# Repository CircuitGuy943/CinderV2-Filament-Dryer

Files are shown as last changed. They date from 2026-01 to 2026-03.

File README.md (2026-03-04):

# Cinder Filament Dryer - A fully featured 90W filament dryer for all your drying needs!

The cinder filament dryer is a self managed ecosystem comprising of 2 45W heaters powered from a 90W+ power supply to provide the most heating power possible. In addition to that, there is also space for 3 possible fans with silica gel pouch to aid in the airflow and dryer performance. Equiped with an SHT40 module, you will always be 110% aware of exactly how long your filament will take to dry and at what temperature and with a 90W heater, I can guarantee that won't be long ;). Also comes in a cool, tilted design with a fancy flame aesthetic on the side, it also utilizes a smart locking system that adapts the arm of the spool holder to the width of the spool hole, this way, you can ensure the spool is free to spin properly and doesn't scratch the heating element. And if that isn't enough filament flow for you, there is also a dedicated servo driving system and filament extrusion rate feedback integration that automatically pushes out the strand of filament so that the printer, or you, don't have to worry about printing while drying. Comes with a 128x64 OLED, 3 buttons and an encoder for all your "control panel" needs because, we all love fancy control panels don't we? The frame itself is designed to be easy to print (albeit quite large) and assemble. And not to mention with the amazing aesthetic comes a super cool futuristic, pod like door system that lifts upwars on a big pin hinge to allow you to remove the spools or insert more. And obviously, we don't want tipping dryers so, on another pin hinge, we have a leg that can be bent backwards flush to the device when the dryer is hung on the wall or extended so that it literally doesn't fall over.

Some CAD images:

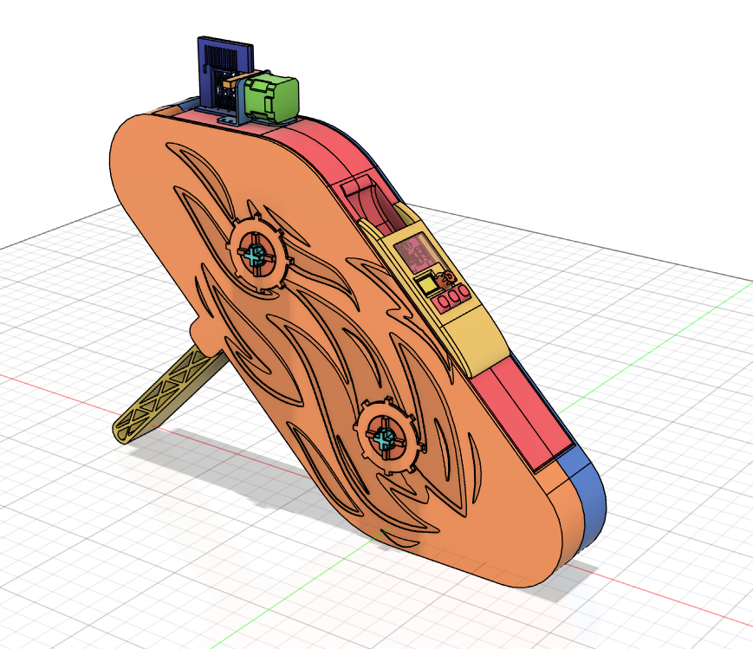
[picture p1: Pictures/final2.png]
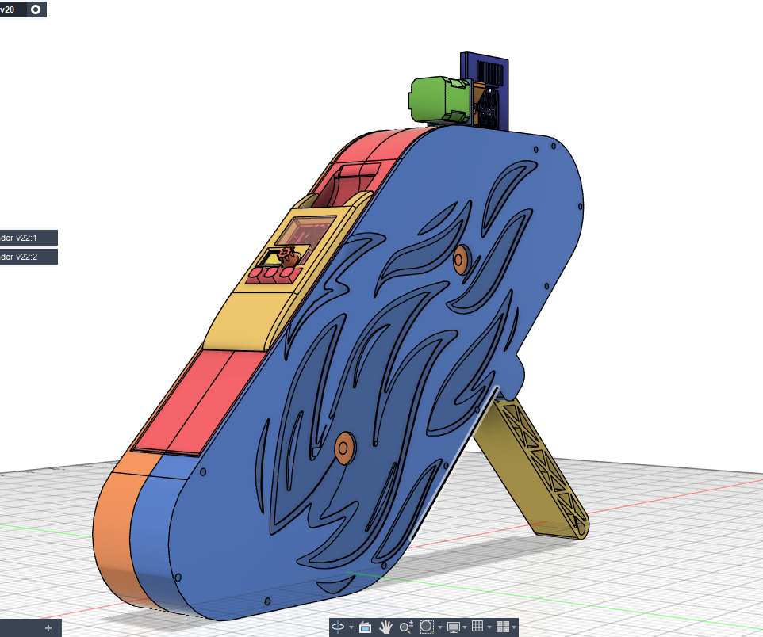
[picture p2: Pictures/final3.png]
 

## Features:
- It drys filament (duh)
- 90W heating power
- OLED display control panel with 3 buttons, encoder and a cool acrylic view panel
- Leg (pretty simple) to hold it from falling backwards
- Fully integrated PCB that drives the 90W heaters, stepper motor driver, OLED, buttons and connectors for all the other sensors.
- Filament pushing system with extruding feedback to maintain proper filament pushing flow
- Easy to assemble
- Airflow powered by 3 5020 fans (LOTS of airflow)
- Spaces for silica gel pouches
- Fancy, cool looking tilted design with flame aesthetics
- Automatic locking system for holding the spool with an arm extendible in diameter <sup>TM</sup>
- PWM control of fans and heater

## PCB
And this is my main PCB. A bit budget restrained otherwise so I had to use some premade sensor modules, the actual flex heater PCB is pretty simple so I won't bother putting it here (but it's in the files):

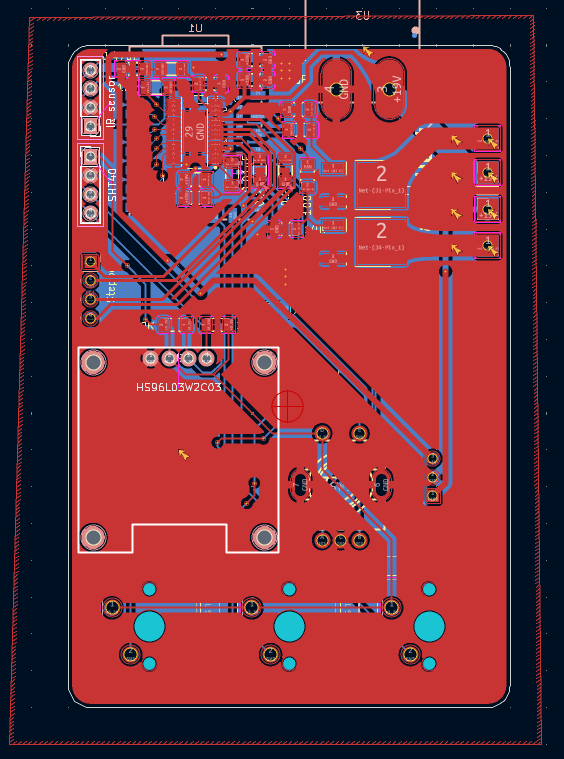
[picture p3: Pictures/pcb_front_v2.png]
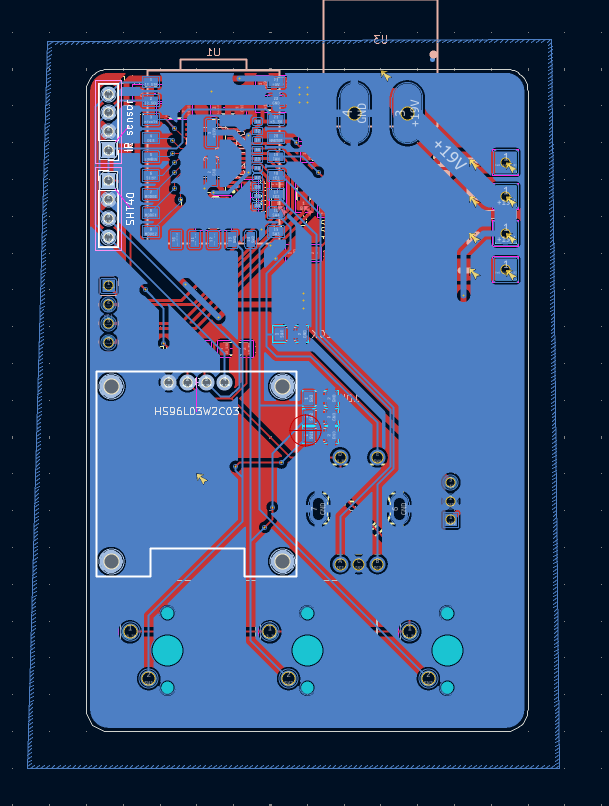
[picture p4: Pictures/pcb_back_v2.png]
  

And the Schematic:

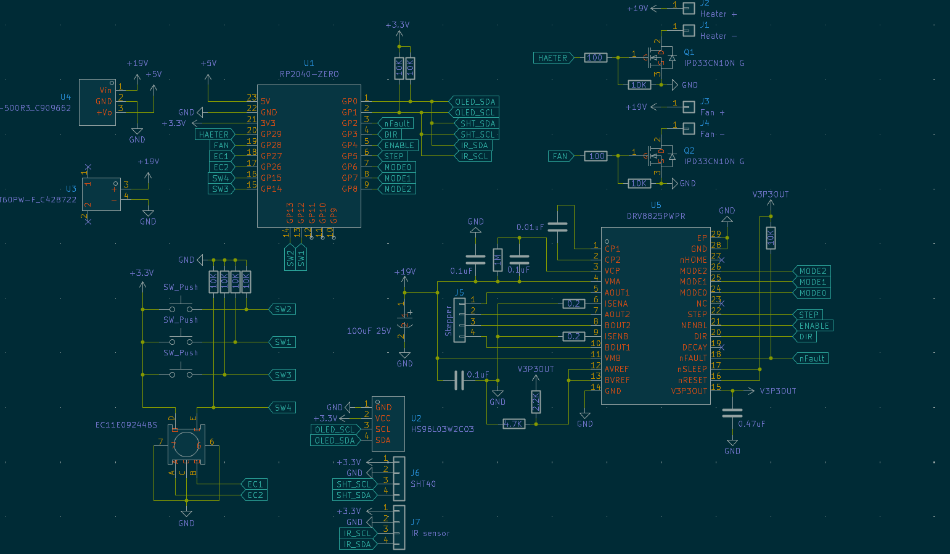
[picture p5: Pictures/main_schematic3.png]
Schematic


And here are some 3D views as well:

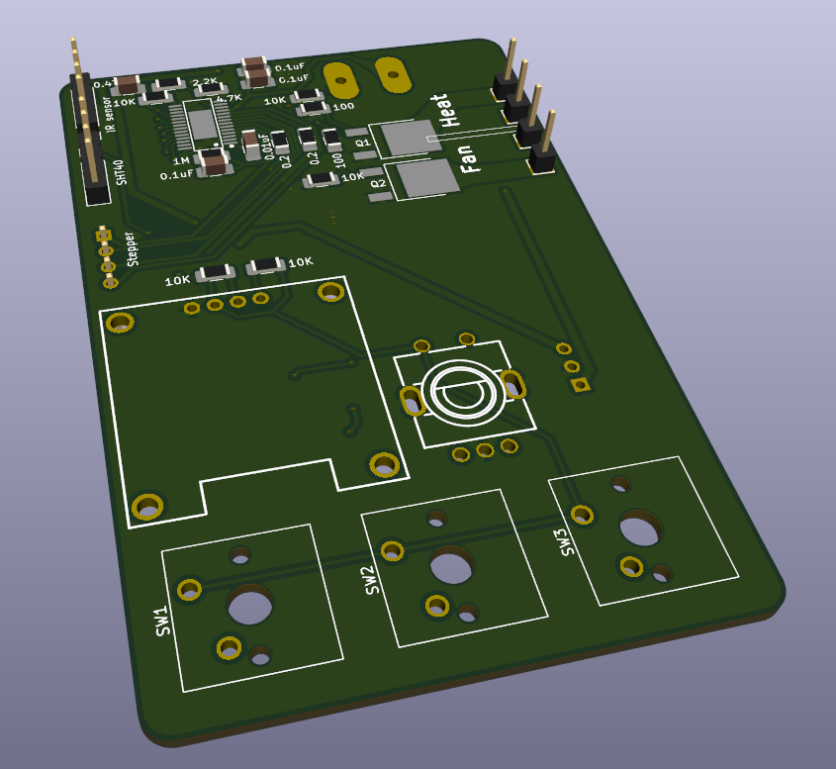
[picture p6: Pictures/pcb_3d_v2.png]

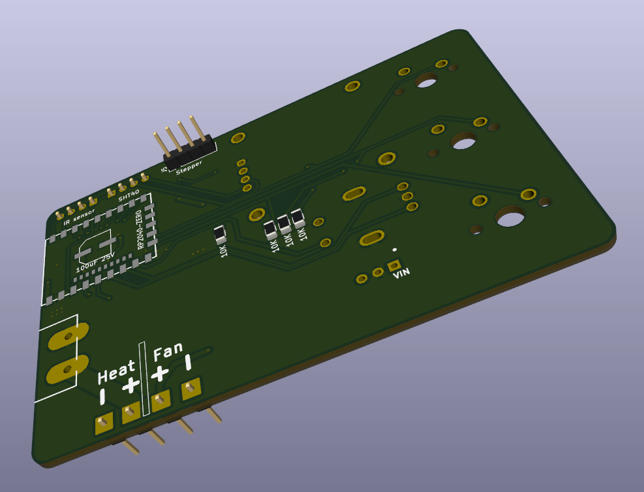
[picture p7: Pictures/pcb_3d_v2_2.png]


## Firmware Overview
At the current moment there is some, untested firmware in there that's supposed to have the dryer functioning but, I don't actually have it yet so I can't test, in future I will program it properly.

## BOM:

- The actual print (alot, probably like 1-2kg+)
- The main PCB (check KiCad files for all the components and external modules)
- 3 5020 fans
- A stepper motor
- Some lasercut acrylic
- MX keycaps (3)
- Some M2 heated inserts and bolts to hold the whole thing togethor

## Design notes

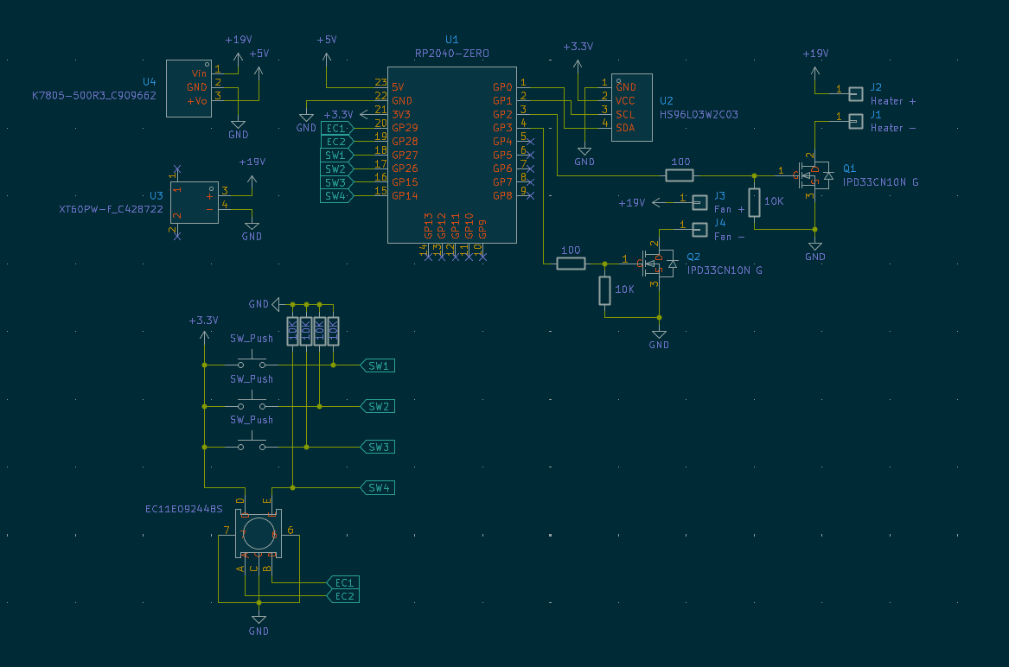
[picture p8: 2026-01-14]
Pictures/main_schematic2.png

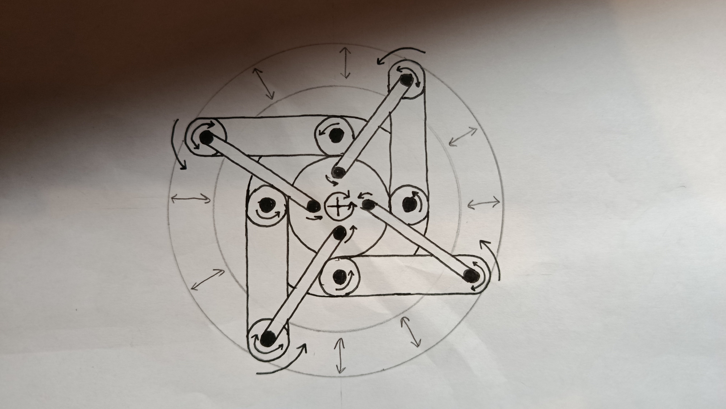
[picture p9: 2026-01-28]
Pictures/design3.jpg

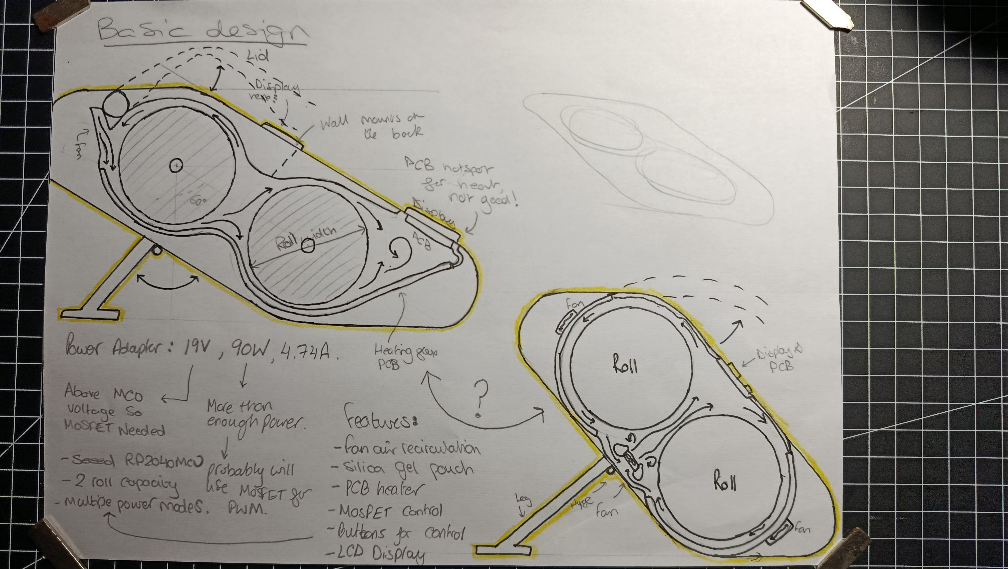
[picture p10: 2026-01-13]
Pictures/design.jpg

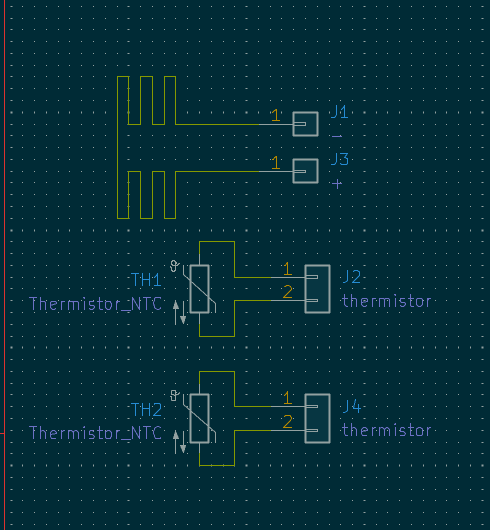
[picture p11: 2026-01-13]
Pictures/flex_heater_schematic.png

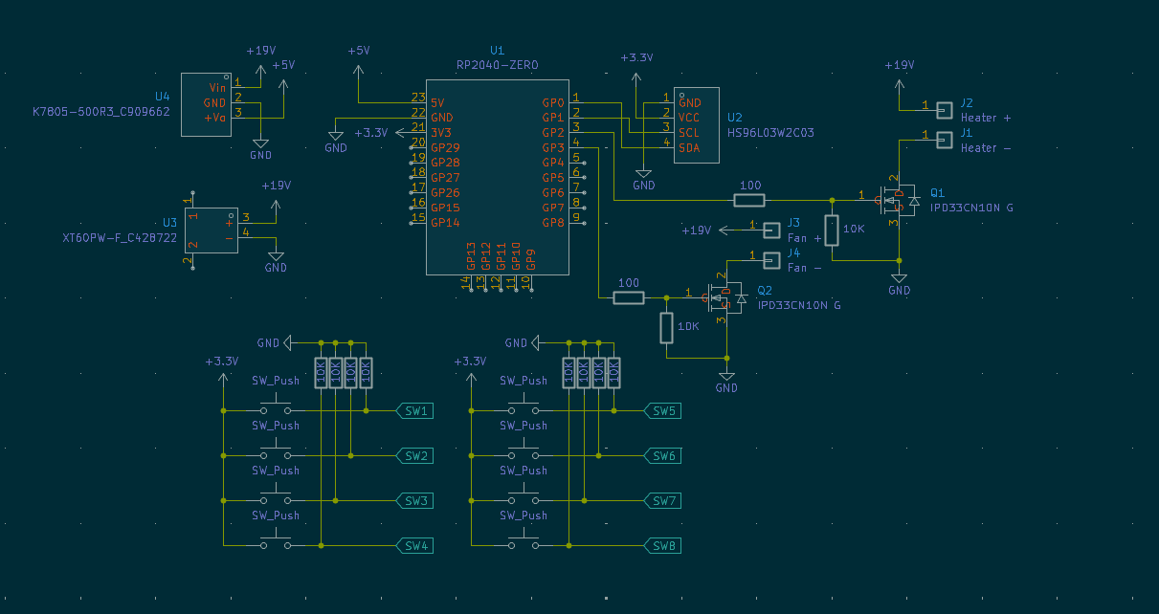
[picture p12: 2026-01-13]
Pictures/main_schematic.png

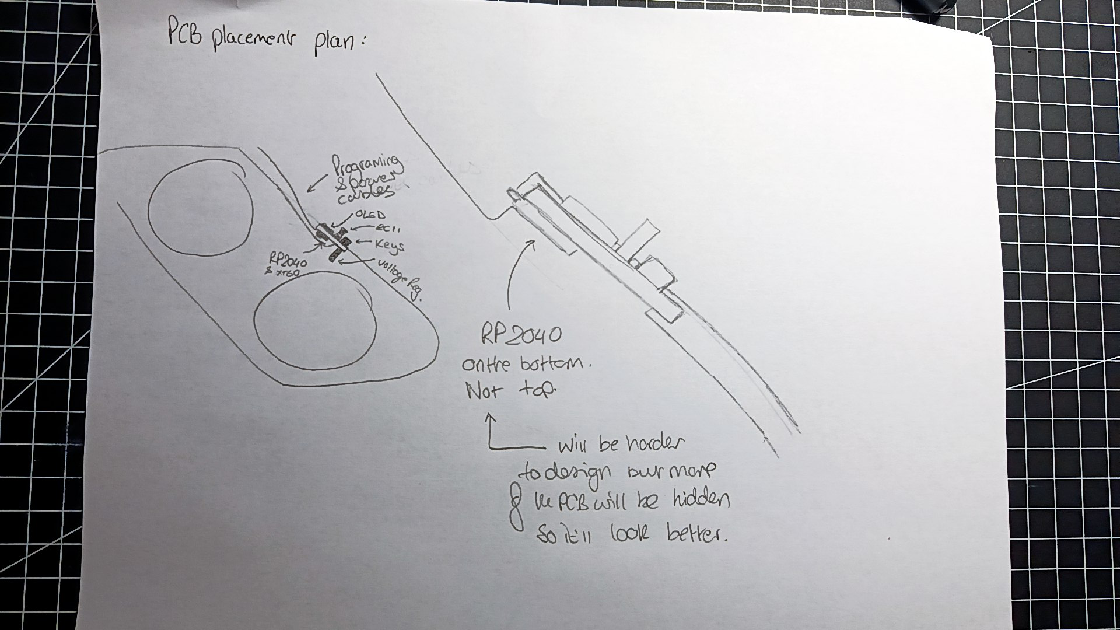
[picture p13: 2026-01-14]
Pictures/design 2.jpg

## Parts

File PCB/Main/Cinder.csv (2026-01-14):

Id | Designator | Footprint | Quantity | Designation | Supplier and ref
1 | J1,J4 | PinHeader_1x01_P2.54mm_Vertical | 2 | -
2 | J2,J3 | PinHeader_1x01_P2.54mm_Vertical | 2 | +
3 | SW1,SW2,SW3 | SW_Cherry_MX_1.00u_PCB | 3 | SW_Push
4 | U1 | COMM-SMD_RP2040-ZERO | 1 | RP2040-ZERO
5 | U2 | OLED-TH_L27.8-W27.2-P2.54_C9900033791 | 1 | HS96L03W2C03
6 | R7,R4,R8,R6,R5,R3 | R_1206_3216Metric_Pad1.30x1.75mm_HandSolder | 6 | 10K
7 | Q2,Q1 | TO-252-2_L6.6-W6.1-P4.57-LS9.9-TL-CW | 2 | IPD33CN10N G
8 | U3 | TH_2P-XT60PW-F | 1 | XT60PW-F_C428722
9 | U4 | PWRM-TH_K78XX-500R3 | 1 | K7805-500R3_C909662
10 | SW9 | SW-TH_EC11XXXXXXXX | 1 | EC11E09244BS
11 | R2,R1 | R_1206_3216Metric_Pad1.30x1.75mm_HandSolder | 2 | 100

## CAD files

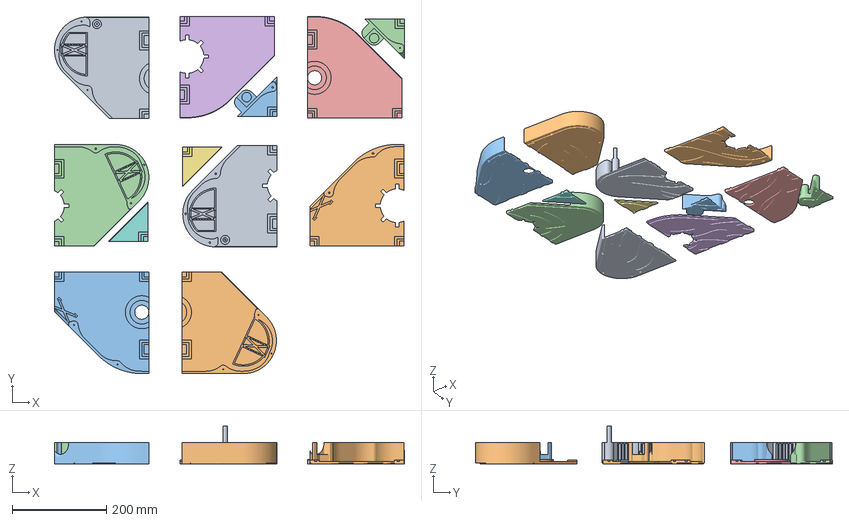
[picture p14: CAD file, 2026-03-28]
Orca Printing Project/Main Body/Project/Main Body.3mf
741.0 x 756.3 x 80.0 mm
Left Side (1).stl
Right Side (6).stl
Right Side (5).stl
Left Side (6).stl
Right Side (2).stl
Left Side (2).stl
Right Side (3).stl
Left Side (3).stl
Right Side (1).stl
Left Side (5).stl
Left Side (4).stl
Right Side (4).stl

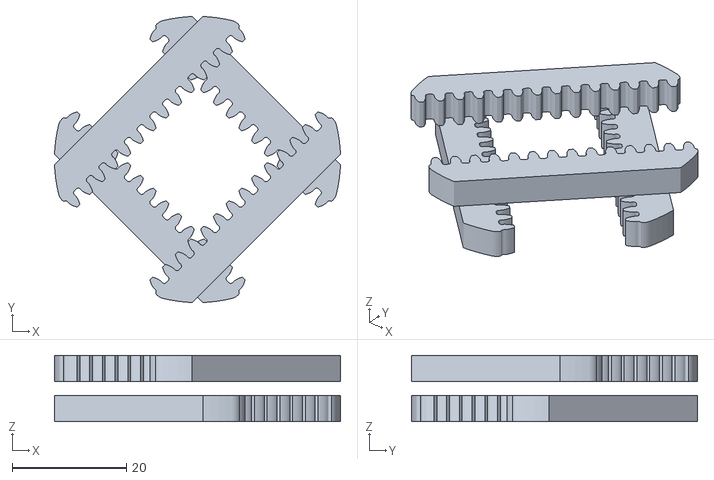
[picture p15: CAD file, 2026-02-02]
CAD Files/Gear Rack Extender/Gear Rack Extender v22_Gear Rack Extender v22_Rack Assembly Offset_1_Rack1_3_Body1.stl
50.0 x 50.0 x 11.6

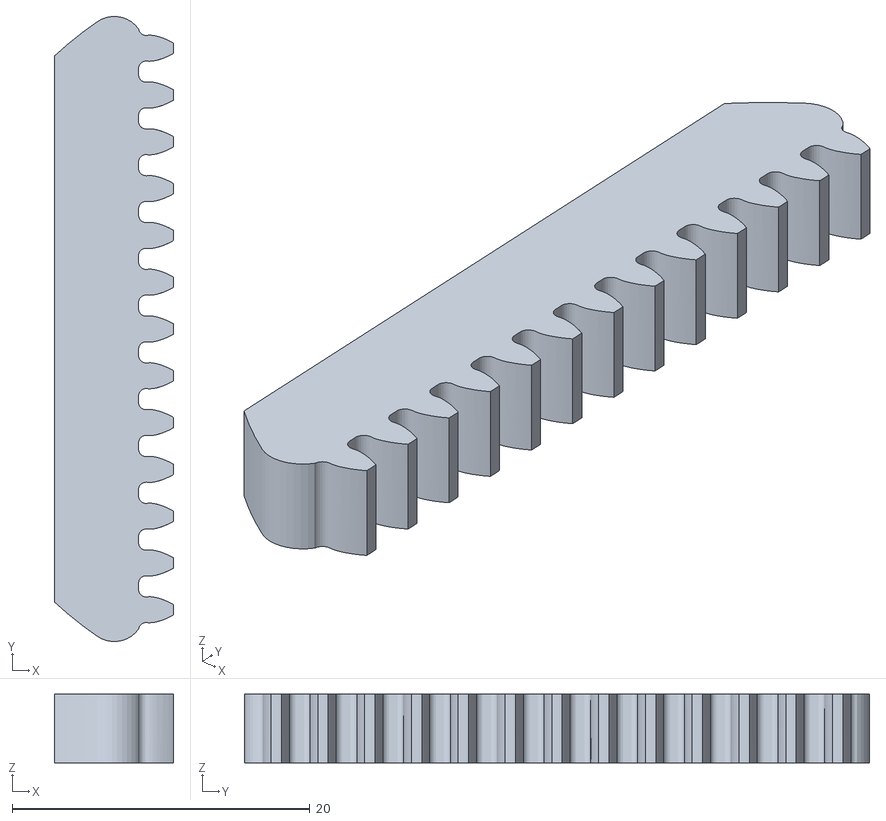
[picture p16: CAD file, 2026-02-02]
CAD Files/Gear Rack Extender/Gear Rack Extender v22_Gear Rack Extender v22_Rack Assembly_4_Rack1 (1)_1_Body1.stl
8.00 x 42.0 x 4.60

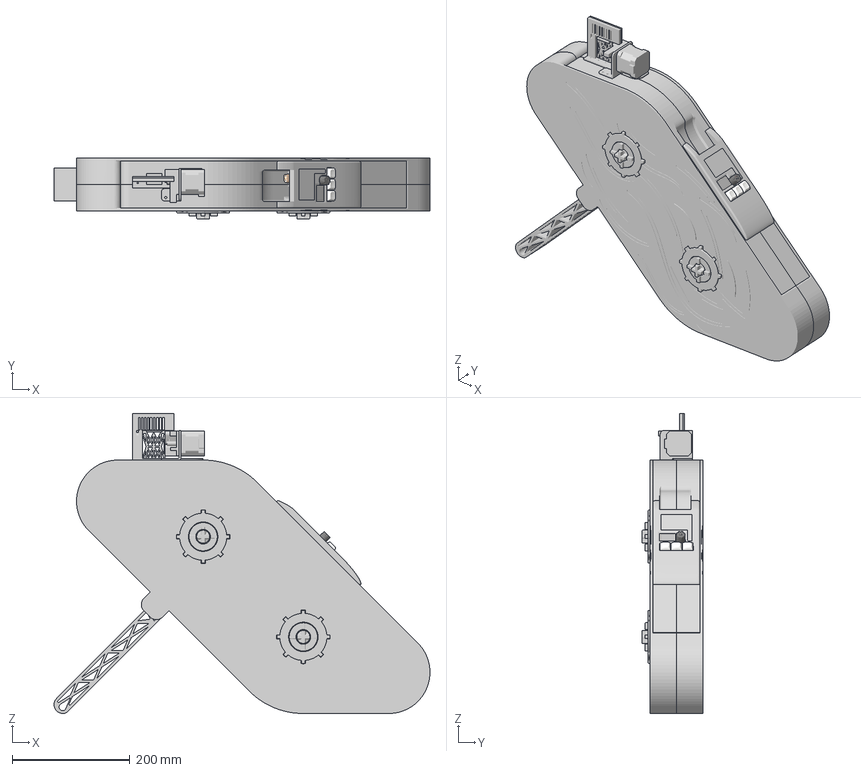
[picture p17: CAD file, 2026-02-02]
CAD Files/Complete Assemblies/3mf Files/Cinder Filament Dryer.3mf
637.9 x 103.2 x 509.0 mm
Acrylic
Bottom Leg (1) x 2
Bottom Leg (2) x 2
Bottom Leg (3) x 2
Bottom Leg x 2
Bottom x 2
Center Pin x 2
Clip Release x 2
Encoder Button
Fan 1
Fan 2
Fan 3
Fan Replacement
Left Door
Left Side
MiddleBot Leg (1) (1) x 2
MiddleBot Leg (1) x 2
MiddleBot Leg (2) x 2
MiddleBot Leg x 2
MiddleTop Leg (1) x 2
MiddleTop Leg x 2
Outer Link (1) x 2
Outer Link x 2
Panel Cover
Pin 1 x 2
Pin 2 x 2
Pin 3 x 2
Pin 4 x 2
Pin Cover x 2
Pin Stopper 1 x 2
Pin Stopper 2 x 2
Pin Stopper 3 x 2
Pin Stopper 4 x 2
Plate (1) x 2
Plate (2) x 2
Plate (3) x 2
Plate (4) x 2
Plate (5) x 2
Plate (6) x 2
Plate x 2
Right Door
Right Side
SHT40
Spool 1
Spool 2
Top Leg (1) x 2
Top Leg (2) x 2
Top Leg (3) x 2
Top Leg x 2
Top x 2

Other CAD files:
CAD Files/Gear Rack Extender/Gear Rack Extender v22_Gear Rack Extender v22_Rack Assembly Offset_2_Rack1_4_Body1.stl
CAD Files/Gear Rack Extender/Gear Rack Extender v22_Gear Rack Extender v22_Rack Assembly_4_Rack3_1_Body1.stl
CAD Files/Gear Rack Extender/Gear Rack Extender v22_Gear Rack Extender v22_Rack Assembly_1_Rack1 (1)_1_Body1.stl
CAD Files/Gear Rack Extender/Gear Rack Extender v22_Gear Rack Extender v22_Rack Assembly_4_Rack2_1_Body1.stl
CAD Files/Gear Rack Extender/Gear Rack Extender v22_Gear Rack Extender v22_Rack Assembly_1_Rack3_1_Body1.stl
CAD Files/Gear Rack Extender/Gear Rack Extender v22_Gear Rack Extender v22_Rack Assembly Offset_2_Rack1_1_Body1.stl
CAD Files/Gear Rack Extender/Gear Rack Extender v22_Gear Rack Extender v22_Rack Assembly_1_Rack2_1_Body1.stl
CAD Files/Gear Rack Extender/Gear Rack Extender v22_Gear Rack Extender v22_Rack Assembly_4_Rack4_1_Body1.stl
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

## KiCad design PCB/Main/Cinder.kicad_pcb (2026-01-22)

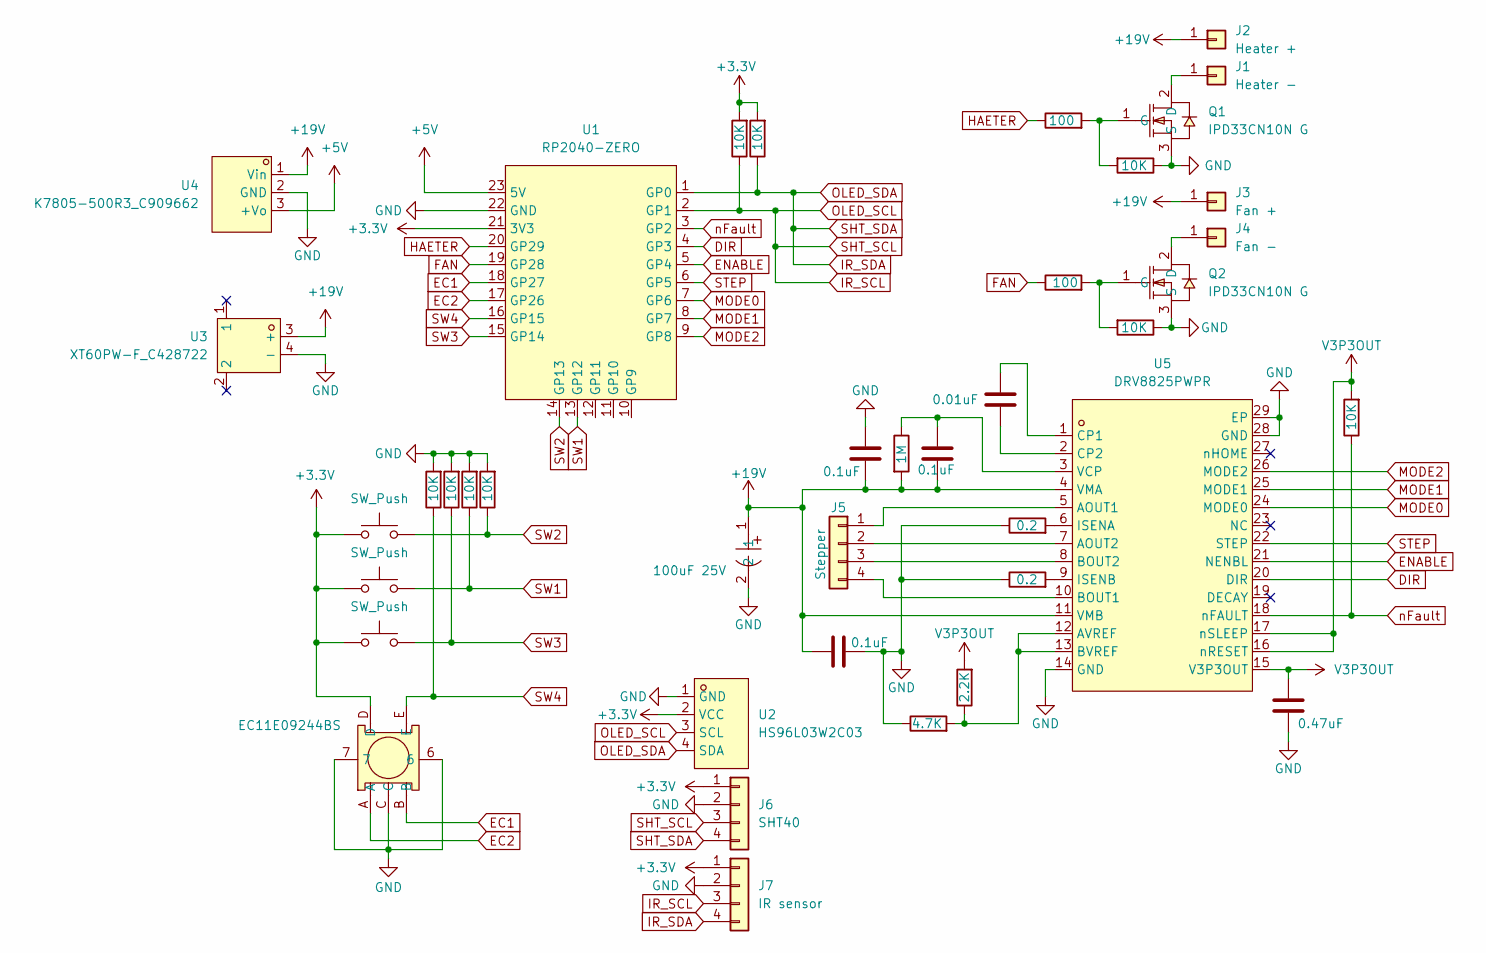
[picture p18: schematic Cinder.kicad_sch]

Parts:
C1: 0.01uF; C_1206_3216Metric_Pad1.33x1.80mm_HandSolder
C2, C3, C4: 0.1uF; C_1206_3216Metric_Pad1.33x1.80mm_HandSolder
C5: 0.47uF; C_1206_3216Metric_Pad1.33x1.80mm_HandSolder
J1: Heater -; PinHeader_1x01_P2.54mm_Vertical
J2: Heater +; PinHeader_1x01_P2.54mm_Vertical
J3: Fan +; PinHeader_1x01_P2.54mm_Vertical
J4: Fan -; PinHeader_1x01_P2.54mm_Vertical
J5: Stepper; PinHeader_1x04_P2.54mm_Vertical
J6: SHT40; PinHeader_1x04_P2.54mm_Vertical
J7: IR sensor; PinHeader_1x04_P2.54mm_Vertical
Q1, Q2: IPD33CN10N G; TO-252-2_L6.6-W6.1-P4.57-LS9.9-TL-CW; LCSC Part C536760
R1, R2: 100; R_1206_3216Metric_Pad1.30x1.75mm_HandSolder
R3, R4, R5, R6, R7, R8, R15, R16, R17: 10K; R_1206_3216Metric_Pad1.30x1.75mm_HandSolder
R9: 1M; R_1206_3216Metric_Pad1.30x1.75mm_HandSolder
R10, R11: 0.2; R_1206_3216Metric_Pad1.30x1.75mm_HandSolder
R12: 2.2K; R_1206_3216Metric_Pad1.30x1.75mm_HandSolder
R13: 4.7K; R_1206_3216Metric_Pad1.30x1.75mm_HandSolder
SW1, SW2, SW3: SW_Push; SW_Cherry_MX_1.00u_PCB
SW9: EC11E09244BS; SW-TH_EC11XXXXXXXX; LCSC Part C470742
U1: RP2040-ZERO; COMM-SMD_RP2040-ZERO; LCSC Part C5350143
U2: HS96L03W2C03; OLED-TH_L27.8-W27.2-P2.54_C9900033791; LCSC Part C5248080
U3: XT60PW-F_C428722; TH_2P-XT60PW-F; LCSC Part C428722
U4: K7805-500R3_C909662; PWRM-TH_K78XX-500R3; LCSC Part C909662
U5: DRV8825PWPR; HTSSOP-28_L9.7-W4.4-P0.65-LS6.4-BL-EP5.5; LCSC Part C81582
U6: 100uF 25V; CAP-SMD_BD6.3-L6.6-W6.6-LS7.2-FD-1; LCSC Part C970685

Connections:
+3.3V: J6.1, J7.1, R16.2, R17.2, SW1.1, SW2.1, SW3.1, SW9.D, U1.21 (3V3), U2.2 (VCC)
+5V: U1.23 (5V), U4.3 (+Vo)
+19V: C2.2, C3.1, C4.1, J2.1, J3.1, R9.2, U3.3 (+), U4.1 (Vin), U5.4 (VMA), U5.11 (VMB), U6.1
DIR: U1.4 (GP3), U5.20 (DIR)
EC1: SW9.B, U1.18 (GP27)
EC2: SW9.A, U1.17 (GP26)
ENABLE: U1.5 (GP4), U5.21 (NENBL)
FAN: R2.1, U1.19 (GP28)
GND: C3.2, C4.2, C5.2, J6.2, J7.2, Q1.3 (S), Q2.3 (S), R3.1, R4.1, R5.2, R6.2, R7.2, R8.2, R10.1, R11.1, R13.1, SW9.6, SW9.7, SW9.C, U1.22 (GND), U2.1 (GND), U3.4 (-), U4.2 (GND), U5.14 (GND), U5.28 (GND), U5.29 (EP), U6.2
HAETER: R1.1, U1.20 (GP29)
IR_SCL: J6.3, J7.3, R16.1, U1.2 (GP1), U2.3 (SCL)
IR_SDA: J6.4, J7.4, R17.1, U1.1 (GP0), U2.4 (SDA)
MODE0: U1.7 (GP6), U5.24 (MODE0)
MODE1: U1.8 (GP7), U5.25 (MODE1)
MODE2: U1.9 (GP8), U5.26 (MODE2)
unnamed: J1.1, Q1.2 (D)
unnamed: J4.1, Q2.2 (D)
unnamed: J5.1, U5.5 (AOUT1)
unnamed: J5.2, U5.7 (AOUT2)
unnamed: J5.3, U5.8 (BOUT2)
unnamed: J5.4, U5.10 (BOUT1)
unnamed: Q1.1 (G), R1.2, R4.2
unnamed: Q2.1 (G), R2.2, R3.2
unnamed: R12.1, R13.2, U5.12 (AVREF), U5.13 (BVREF)
unnamed: C1.1, U5.1 (CP1)
unnamed: C1.2, U5.2 (CP2)
unnamed: R10.2, U5.6 (ISENA)
unnamed: R11.2, U5.9 (ISENB)
unnamed: C2.1, R9.1, U5.3 (VCP)
STEP: U1.6 (GP5), U5.22 (STEP)
SW1: R6.1, SW1.2, U1.13 (GP12)
SW2: R5.1, SW2.2, U1.14 (GP13)
SW3: R7.1, SW3.2, U1.15 (GP14)
SW4: R8.1, SW9.E, U1.16 (GP15)
V3P3OUT: C5.1, R12.2, R15.2, U5.15 (V3P3OUT), U5.16 (nRESET), U5.17 (nSLEEP)
nFault: R15.1, U1.3 (GP2), U5.18 (nFAULT)

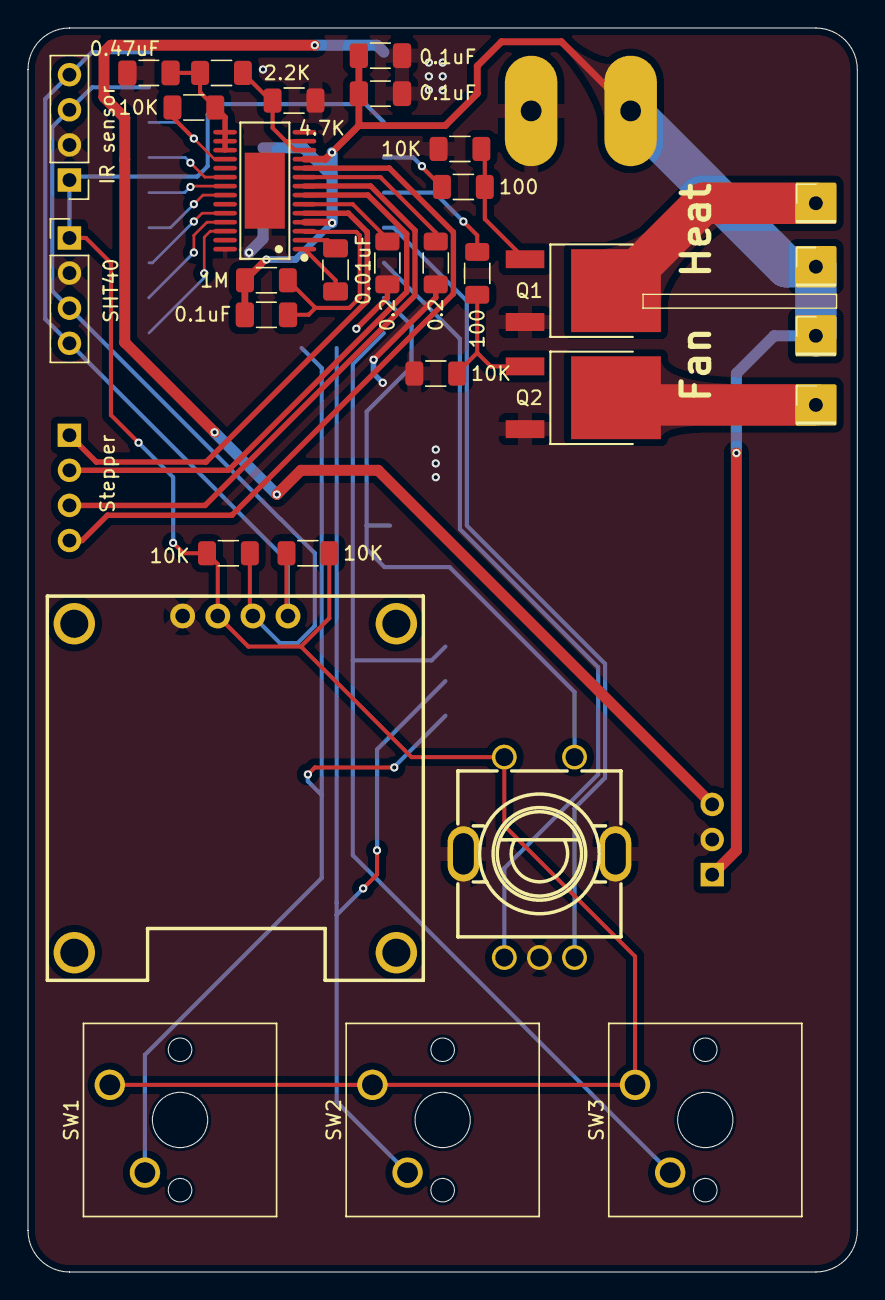
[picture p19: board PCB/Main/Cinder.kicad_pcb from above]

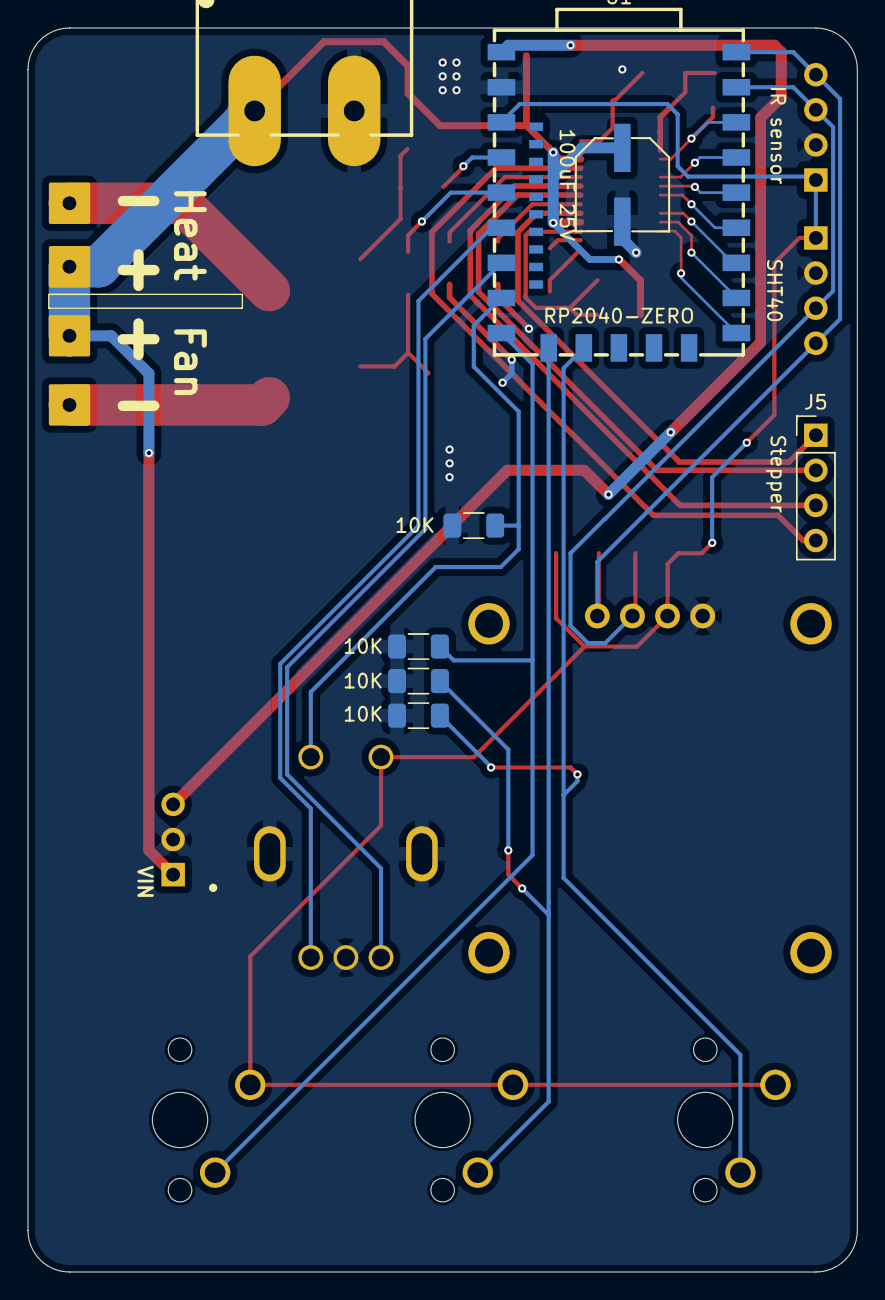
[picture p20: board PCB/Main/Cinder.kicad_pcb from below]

Board: 2 copper layers, 60.0 x 90.0 mm, 40 parts (9 on the bottom side), 36 nets.

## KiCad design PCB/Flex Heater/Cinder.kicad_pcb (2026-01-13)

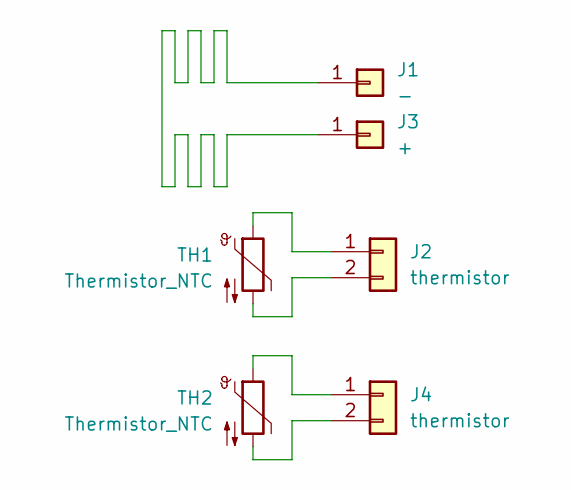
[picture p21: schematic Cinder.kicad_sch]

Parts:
J1: -; PinHeader_1x01_P1.00mm_Vertical
J2, J4: thermistor; PinHeader_1x02_P1.00mm_Vertical
J3: +; PinHeader_1x01_P1.00mm_Vertical
TH1, TH2: Thermistor_NTC; R_0603_1608Metric

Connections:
unnamed: J1.1, J3.1
unnamed: J2.1, TH1.1
unnamed: J2.2, TH1.2
unnamed: J4.1, TH2.1
unnamed: J4.2, TH2.2

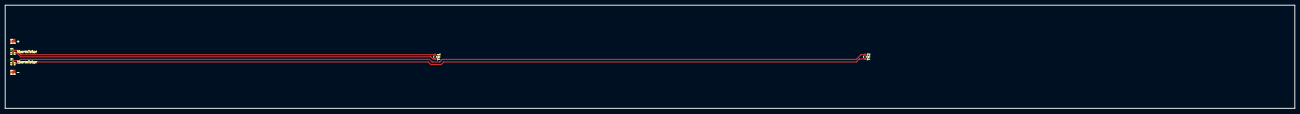
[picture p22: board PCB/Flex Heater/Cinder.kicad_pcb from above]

Board: 2 copper layers, 500.0 x 40.0 mm, 6 parts (0 on the bottom side), 5 nets.

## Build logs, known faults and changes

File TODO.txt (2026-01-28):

1. Ensure that when stepper runs, heater is turned off/power reduced to ensure power is controlled.
3. Add filament pusher
4. Make sure all tolerances are there for printing moving and sticking together parts

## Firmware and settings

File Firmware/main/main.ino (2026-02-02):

#include <Encoder.h>
#include <Bounce2.h>
#define DUMP_REGS
#include <Wire.h>
#include <APDS9930.h>

#include <Arduino.h>
#include <U8g2lib.h>

#ifdef U8X8_HAVE_HW_SPI
#include <SPI.h>
#endif
#ifdef U8X8_HAVE_HW_I2C
#include <Wire.h>
#endif

// Define pins
const int heater = 29;  // Timer0
const int fan = 28;  // Timer0 or Timer1 depending on board


Encoder myEnc(26, 27);

APDS9930 apds = APDS9930();
uint16_t proximity_data = 0;

// ================== BUTTONS ==================
Bounce btn1;
Bounce btn2;
Bounce btn3;
Bounce btn4;

constexpr uint8_t BTN_1_PIN = 12;
constexpr uint8_t BTN_2_PIN = 13;
constexpr uint8_t BTN_3_PIN = 14;
constexpr uint8_t BTN_4_PIN = 15;
// ================================================

AccelStepper stepper(AccelStepper::DRIVER, 5, 2);
const int enable_pin = 4;
const int mode0 = 6;
const int mode1 = 7;
const int mode2 = 8;



void setupButtons() {
  pinMode(BTN_1_PIN, INPUT);
  pinMode(BTN_2_PIN, INPUT);
  pinMode(BTN_3_PIN, INPUT);
  pinMode(BTN_4_PIN, INPUT);

  btn1.attach(BTN_1_PIN);
  btn2.attach(BTN_2_PIN);
  btn3.attach(BTN_3_PIN);
  btn4.attach(BTN_4_PIN);

  btn1.interval(10);
  btn2.interval(10);
  btn3.interval(10);
  btn4.interval(10);
}
void filamentSensorSetup() {
  Serial.println(F("---------------------------"));
  Serial.println(F("APDS-9930 - ProximitySensor"));
  Serial.println(F("---------------------------"));

  if ( apds.init() ) {
    Serial.println(F("APDS-9930 initialization complete"));
  } else {
    Serial.println(F("Something went wrong during APDS-9930 init!"));
  }

  // // Adjust the Proximity sensor gain
  // if ( !apds.setProximityGain(PGAIN_2X) ) {
  //   Serial.println(F("Something went wrong trying to set PGAIN"));
  // }

  if ( apds.enableProximitySensor(false) ) {
    Serial.println(F("Proximity sensor is now running"));
  } else {
    Serial.println(F("Something went wrong during sensor init!"));
  }
}
#ifdef DUMP_REGS
  /* Register dump */
  uint8_t reg;
  uint8_t val;

  for(reg = 0x00; reg <= 0x19; reg++) {
    if( (reg != 0x10) && \
        (reg != 0x11) )
    {
      apds.wireReadDataByte(reg, val);
      Serial.print(reg, HEX);
      Serial.print(": 0x");
      Serial.println(val, HEX);
    }
  }
  apds.wireReadDataByte(0x1E, val);
  Serial.print(0x1E, HEX);
  Serial.print(": 0x");
  Serial.println(val, HEX);
#endif
}
void oledSetup(): {
  U8G2_SSD1306_128X64_NONAME_F_HW_I2C u8g2(U8G2_R0, /* reset=*/ U8X8_PIN_NONE);
  u8g2.begin();
}
void shtSetup(): {
  while (!Serial)
    delay(10);     // will pause Zero, Leonardo, etc until serial console opens

  Serial.println("Adafruit SHT4x test");
  if (! sht4.begin()) {
    Serial.println("Couldn't find SHT4x");
    while (1) delay(1);
  }
  Serial.println("Found SHT4x sensor");
  Serial.print("Serial number 0x");
  Serial.println(sht4.readSerial(), HEX);

  // You can have 3 different precisions, higher precision takes longer
  sht4.setPrecision(SHT4X_HIGH_PRECISION);
  switch (sht4.getPrecision()) {
     case SHT4X_HIGH_PRECISION: 
       Serial.println("High precision");
       break;
     case SHT4X_MED_PRECISION: 
       Serial.println("Med precision");
       break;
     case SHT4X_LOW_PRECISION: 
       Serial.println("Low precision");
       break;
  }

  // You can have 6 different heater settings
  // higher heat and longer times uses more power
  // and reads will take longer too!
  sht4.setHeater(SHT4X_NO_HEATER);
  switch (sht4.getHeater()) {
     case SHT4X_NO_HEATER: 
       Serial.println("No heater");
       break;
     case SHT4X_HIGH_HEATER_1S: 
       Serial.println("High heat for 1 second");
       break;
     case SHT4X_HIGH_HEATER_100MS: 
       Serial.println("High heat for 0.1 second");
       break;
     case SHT4X_MED_HEATER_1S: 
       Serial.println("Medium heat for 1 second");
       break;
     case SHT4X_MED_HEATER_100MS: 
       Serial.println("Medium heat for 0.1 second");
       break;
     case SHT4X_LOW_HEATER_1S: 
       Serial.println("Low heat for 1 second");
       break;
     case SHT4X_LOW_HEATER_100MS: 
       Serial.println("Low heat for 0.1 second");
       break;
  }
  
}


void setup() {
  Wire.setSDA(0);
  Wire.setSCL(1);

  oledSetup();

  filamentSensorSetup();

  shtSetup();

  setupButtons();

  pinMode(heater, OUTPUT);
  pinMode(fan, OUTPUT);

  pinMode(enable_pin, OUTPUT);

  stepper.setMaxSpeed(1000); // steps/sec
  stepper.setAcceleration(500); // steps/sec^2

  Serial.begin(9600);
  Serial.println("Basic Functionality Firmware");
}


void updateButtons() {
  btn1.update();
  btn2.update();
  btn3.update();
  btn4.update();

  if (btn1.fell()) onButton1Press();
  if (btn2.fell()) onButton2Press();
  if (btn3.fell()) onButton3Press();
  if (btn4.fell()) onButton4Press();
}
void updateEncoder() {
  long newPosition = myEnc.read();
  if (newPosition != oldPosition) {
    oldPosition = newPosition;
    Serial.println("Encoder Position: " + str(newPosition));
  }
}
void updateOLED(): {
  u8g2.clearBuffer();					// clear the internal memory
  u8g2.setFont(u8g2_font_ncenB08_tr);	// choose a suitable font
  u8g2.drawStr(0,10,"Hello World!");	// write something to the internal memory
  u8g2.sendBuffer();					// transfer internal memory to the display
}
void readProximitySensor(): {
  if ( !apds.readProximity(proximity_data) ) {
  Serial.println("Error reading proximity value");
  }
  else {
  Serial.print("Proximity: ");
  Serial.println(proximity_data);
  }
}
void readSHT40(): {
  sensors_event_t humidity, temp;
  
  uint32_t timestamp = millis();
  sht4.getEvent(&humidity, &temp);// populate temp and humidity objects with fresh data
  timestamp = millis() - timestamp;

  Serial.print("Temperature: "); Serial.print(temp.temperature); Serial.println(" degrees C");
  Serial.print("Humidity: "); Serial.print(humidity.relative_humidity); Serial.println("% rH");

  Serial.print("Read duration (ms): ");
  Serial.println(timestamp);
}


long oldPosition  = -999;

void loop() {
  updateEncoder():
  updateButtons();
  updateOLED();
  readProximitySensor();
  readSHT40(); 
  analogWrite(heater, 64); // 25% duty cycle
  analogWrite(fan, 192); // 75% duty cycle

  digitalWrite(enable_pin, LOW);
  digitalWrite(mode0, HIGH);
  digitalWrite(mode1, LOW);
  digitalWrite(mode2, LOW);
  stepper.moveTo(100); // move 2000 steps
  stepper.run();
  delay(1000);
}





void onButton1Press() {
  Serial.println("Button 1 pressed");
}

void onButton2Press() {
  Serial.println("Button 2 pressed");
}

void onButton3Press() {
  Serial.println("Button 3 pressed");
}

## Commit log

2026-01-14 Update - Done main PCB
    [Cinder-B_Cu.gbr, Cinder-B_Mask.gbr, Cinder-B_Paste.gbr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]
2026-02-02 Update with CAD files and pictures
    [Acrylic.stl, Cinder Filament Dryer v20.step, Cinder Filament Dryer v20_Cinder Filament Dryer v20_Door_1_Extruder_1_Body1.stl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]
2026-02-02 Revise README for Cinder Filament Dryer details
    Updated the README to provide a detailed description of the Cinder Filament Dryer, including features, PCB information, firmware overview, and BOM.
2026-02-02 Update README with CAD and PCB images
    Added CAD images and updated PCB images in README.
2026-02-02 Enhance README with dryer details and images
    Added detailed description of the cinder filament dryer and included images.
